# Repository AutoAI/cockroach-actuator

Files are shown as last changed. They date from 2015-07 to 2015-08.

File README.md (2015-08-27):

# baja-actuator
This is an arduino project that interfaces with the rest of the DriveAI-Platform and actuates the vehicle according to the commands passed to it via serial. 

##Synchronization
The control section operates asynchronously from the rest of the computer, and has a variable refresh rate. By default, the controller updates at 100Hz. Serial can be sent to the controller at any time, and is collected and applied during the next cycle. At the default refresh rate, this results in around 10-12ms of latency in a worst-case scenario. This is suitably fast for driving at low speeds, and can be made much faster as needed.

##Encoding and Transmission
Each time the controller is sent a command, it is in the form of one byte of data. We have written an encoder for said data that provides a balance between raw speed and movement precision. Each packet looks like this:

control diagram

The first two bits of data indicate which control element is being set. This configuration allows for up to 4 individual controls, which we have assigned as follows:
  - 0b**00** - Stop the engine immediately.
  - 0b**01** - Control steering.
  - 0b**10** - Control acceleration.
  - 0b**11** - Control braking.
  
The last 6 bits of data represent the position value being written to that control. This translates to an unsigned integer from 0-63. We believe that 64 positions per control is adequate for our current vehicle. It is our intention in the future to increase the precision of these controls for use in larger vehicles. Therefore, the currently established ranges for the controls in hexadecimal are as follows:
  - 0x**00** to 0x**3F** - Stop the engine immediately.
  - 0x**40** to 0x**7F** - Control steering, with 0x**40** being extreme left, and 0x**7F** being extreme right.
  - 0x**80** to 0x**BF** - Control acceleration, with 0x**80** being full throttle, and 0x**BF** being zero throttle.
  - 0x**c0** to 0x**FF** - Control steering, with 0x**C0** being no braking, and 0x**FF** being full power braking.

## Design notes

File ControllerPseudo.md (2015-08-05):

```
//CODE FOR CONTROLLING THE GO-KART

<include servo.h>

const int ENGINE_PIN = 7;
const int GAS_PIN = 6;

const int BRAKE_VELOCITY_PIN = 3;
const int BRAKE_DIRECTION_PIN = 2;
const int BRAKE_SENSE_PIN = 1;

const int STEERING_VELOCITY_PIN = 5;
const int STEERING_DIRECTION_PIN = 4;
const int STEERING_SENSE_PIN = 0;

int steeringPosition = 0;
int brakingPosition = 0;

int steeringGoal = 512;
int brakingGoal = 0;
int accelerationGoal = 0;

boolean steeringChanged = false;
boolean brakingChanged = false;
boolean accelerationChanged = false;

int power = 255;
int threshold = 25;
int angle = 0;

void setup {
	Servo gas; //create the servo object
	gas.attach(GAS_PIN); //bind it to the throttle pin
	
	pinMode (STEERING_VELOCITY_PIN, OUTPUT); //set all the relevant pins to output
	pinMode (STEERING_DIRECTION_PIN, OUTPUT);
	pinMode (BRAKING_VELOCITY_PIN, OUTPUT);
	pinMode (BRAKING_DIRECTION_PIN, OUTPUT);
	pinMode (ENGINE_PIN, OUTPUT);
	
	Serial.begin(9600); //start the serial transmitter
	digitalWrite (ENGINE_PIN, LOW);
	Serial.println("Initialization Completed.");
}

void loop {
	if(Serial.available())
		decodeInput(Serial.read());
		
	if (steeringChanged) {
		setSteering(steeringGoal);
	}
	
	if (brakingChanged) {
		setBrake(brakingGoal);
	}
	
	if (accelerationChanged) {
		setAcceleration(acclerationGoal);
	}
	
	delay(10);
}

void decodeInput(int input) {
  int function = input >> 6; //take only the first 2 bits
  int value = input & 0x3F; //take only the last 6 bits
  if (function == 1) {
    steeringGoal = value * 16;
    steeringChanged = true;
  } else if (function == 2) {
      accelerationGoal = value;
      accelerationChanged = true;
  } else if (function == 3) {
      brakingGoal = value * 16;
      brakingChanged = true;
  } else {
    digitalWrite(ENGINE_PIN, HIGH);
    Serial.println("Killing Engine!");
  }
}

void setSteering(int goal) {
	steeringPosition = analogRead(STEERING_SENSE_PIN);
	if (abs(steeringPosition-goal) <= threshold) {
    		analogWrite(STEERING_VELOCITY_PIN, 0);
    		steeringChanged = false;
	} else if (steeringPosition < goal) { // always move toward the value
    		digitalWrite(STEERING_DIRECTION_PIN, HIGH);
    		analogWrite(STEERING_VELOCITY_PIN, power);
  	} else {
    		digitalWrite(STEERING_DIRECTION_PIN, LOW);
    		analogWrite(STEERING_VELOCITY_PIN, power);
	} 
}

void setBrake(int goal) {
	brakingPosition = analogRead(BRAKING_SENSE_PIN);
	if (abs(brakingPosition-goal) <= threshold) {
    		analogWrite(BRAKING_VELOCITY_PIN, 0);
    		brakingChanged = false;	
	} else if (brakingPosition < goal) { // always move toward the value
    		digitalWrite(BRAKING_DIRECTION_PIN, HIGH);
    		analogWrite(BRAKING_VELOCITY_PIN, power);
  	} else {
    		digitalWrite(BRAKING_DIRECTION_PIN, LOW);
    		analogWrite(BRAKING_VELOCITY_PIN, power);
	} 
}

void setAcceleration(int goal) {
	if (angle < goal*2) { // always move toward the value
		gas.write(angle);
   		angle++;
  	} else if (angle > goal*2) {
    		gas.write(angle);
    		angle--;
  	}
}
```

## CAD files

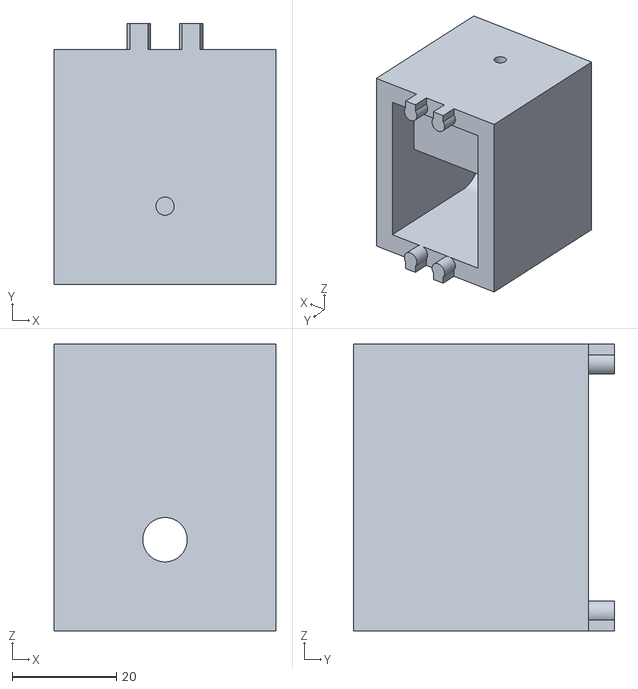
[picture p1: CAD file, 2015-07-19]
parts/bridge 2.stl
42.5 x 50.0 x 55.0

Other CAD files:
parts/bridge.dwg

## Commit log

2015-07-01 added readme that details basic flow of data
2015-07-03 added arduino serial test
2015-07-05 added a throttle sweep
2015-07-06 Added bridge part for the throttle servo
    [bridge.dwg]
2015-07-06 Fixes #1
    [bridge 2.stl, bridge.dwg]
2015-07-19 actuated the new motor shields
2015-08-05 Create ControllerPseudo.md
    Initial Pseudocode for controlling the go-kart. The steering and brakes use linear actuators with potentiometers on them, and the throttle is controlled by a servo.
2015-08-27 Fixed the pin numbers and directional settings for the new kart wiring.
    [KartController.ino]
